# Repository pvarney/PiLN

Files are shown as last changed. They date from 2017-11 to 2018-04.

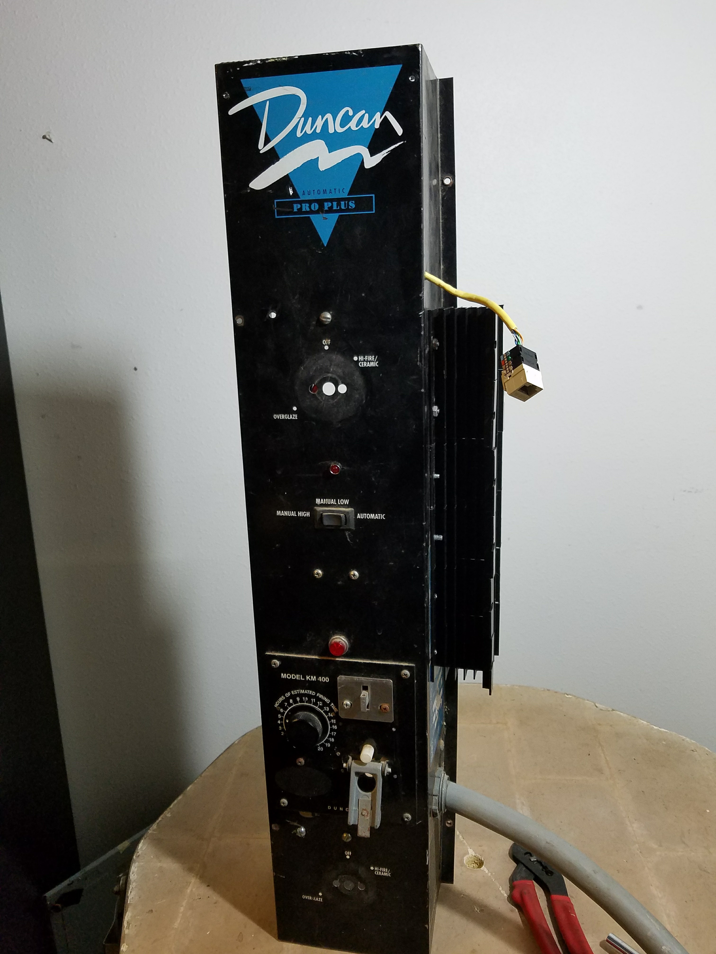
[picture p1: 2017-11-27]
Hardware2.jpg

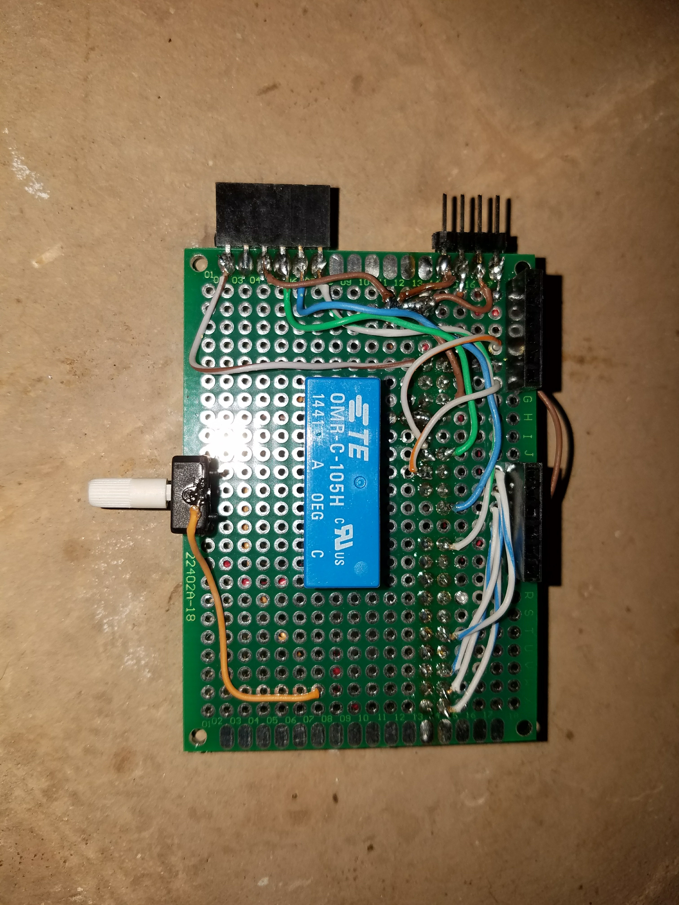
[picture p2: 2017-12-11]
Hardware6.jpg

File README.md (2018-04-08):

# PiLN
Web-based Raspberry Pi Kiln Control Application

This is my first foray into Python, Git, RPi, etc - Please be kind ;-)

I have a good size 220v 45amp electric kiln that has the old "kiln-sitter" style temperature control with bi-metal on/off cycle adjustment knobs. I wanted something with much more precise temperature control for more consistent results and in order to do more work with glass. I started this project with an Arduino board but found the wifi connectivity and coding much too complicated. Being rather proficient in Perl, it seemed the RPi was a better solution. I wrote the original PID control in Perl, but then ported to Python since there seemed to be much more support for it on the RPi and since it was something I wanted to learn anyway.

WARNING! Electricity and heat are dangerous! Please be careful and seek professional help if you are not experienced dealing with high voltage and heat. Use this code/information at your own risk.

This is what I hoped to accomplish:

- Create a PID controller in Python to control an electric kiln. The program takes target temperature, rate, hold time and interval seconds as inputs.
- Daemonize it
- Use MySQL to track temperature change, firing profiles, etc
- Chart the results of firing in real time with google charts
- Wrap in all in a web front end

Many many many thanks to all those who post helpful tidbits out on the web - those on stackoverflow.com in particular. Way to many bits and pieces to give any particular credit. However, I did pull PID calculation code from the following to replace my own code that was iffy (what's math?). It was in C, but was an easy port to Python:

http://brettbeauregard.com/blog/2011/04/improving-the-beginner%E2%80%99s-pid-reset-windup/

All comments, questions, contributions and suggestions welcome!

Future improvements:
- Better calculation of remaining segment time. Currently, remaining time is reset to hold time once temperature is reached.
- Crash/loss of power recovery
- Overheat shutdown

Install:
- Hardware: Raspberry Pi 3, MAX31855 thermocouple interface from Adafruit (https://www.adafruit.com/product/269), High temperature (2372 F) type K thermocouple (http://r.ebay.com/a4cHY1 - search for "kiln thermocouple"), 6 x 40amp Solid State Relays - 2 for each heating element (http://a.co/8PtFgIr), 4 x 20 LCD Display (https://www.adafruit.com/product/198), 5v reed or solid state relay (low voltage load) used to switch 5v supply to high load SSRs (note that the 5v reed relay I used is switched successfully using the 3.3v supply of the GPIO pins), LED for relay on indicator, resistor for LED, variable resistor for LCD contrast adjustment.

- Pin-Out:

		MAX31855+:		3.3v, Pin 1
		MAX31855-:		GROUND, Pin 20
		MAX31855 CLK:		GPIO 25, Pin 22
		MAX31855 CS:		GPIO 24, Pin 18
		MAX31855 DO:		GPIO 18, Pin 12
		REED RELAY+: 		GPIO 4, Pin 7
		REED RELAY-:		GROUND, Pin 20
		REED RELAY INPUT: 	5v, Pin 2
		REED RELAY OUTPUT:	To LED, and high power SSRs (see Fritzing diagram)
		LCD Vss: 		GROUND, Pin 20
		LCD Vcc: 		5v, Pin 2
		LCD Vo: 		Variable Resistor
		LCD RS: 		GPIO 17, Pin 11
		LCD R/W: 		GROUND, Pin 20
		LCD E:			GPIO 27, Pin 13
		LCD DB4:		GPIO 12, Pin 32
		LCD DB5:		GPIO 16, Pin 36
		LCD DB6:		GPIO 20, Pin 38
		LCD DB7:		GPIO 21, Pin 40
		LCD LED+:		5v, Pin 2
		LCD LED-:		GROUND, Pin 20

- Install PiLN files in /home and create log directory:

		cd /home
		sudo git clone https://github.com/pvarney/PiLN
		sudo mkdir /home/PiLN/log
		
- Install MySQL/PHPMyAdmin (PHPMyAdmin not required):

		sudo apt-get install mysql-server
		sudo apt-get install mysql-client php5-mysql
		sudo apt-get install phpmyadmin
		
- Set up Apache for PHPMyAdmin if required. Edit /etc/apache2/apache2.conf and add the follow at the bottom of the file:
	
		Include /etc/phpmyadmin/apache.conf
		
- Set up directories/link for web page:

		sudo mkdir /var/www/html/images	
		sudo mkdir /var/www/html/style	
		sudo ln -s /home/PiLN/images/hdrback.png /var/www/html/images/hdrback.png	
		sudo ln -s /home/PiLN/images/piln.png /var/www/html/images/piln.png	
		sudo ln -s /home/PiLN/style/style.css /var/www/html/style/style.css
	
- Add the following ScriptAlias and Directory parameters under "IfDefine ENABLE_USR_LIB_CGI_BIN" in /etc/apache2/conf-available/serve-cgi-bin.conf:
	
		ScriptAlias /pilnapp/ /home/PiLN/app/
		  <Directory "/home/PiLN/app/">
		    AllowOverride None
		    Options +ExecCGI -MultiViews +SymLinksIfOwnerMatch
		    Require all granted
		  </Directory>

- Create links to enable cgi modules:
	
		cd /etc/apache2/mods-enabled
		sudo ln -s ../mods-available/cgid.conf cgid.conf
		sudo ln -s ../mods-available/cgid.load cgid.load
		sudo ln -s ../mods-available/cgi.load cgi.load

- Restart Apache:
	
		sudo systemctl daemon-reload
		sudo systemctl restart apache2
		
- Install required Python packages:
		
		sudo apt-get install python-mysqldb
		sudo apt-get install python-dev
		sudo pip install PyMySQL
		
- Install Adafruit MAX31855 Module:

		cd ~
		git clone https://github.com/adafruit/Adafruit_Python_MAX31855.git
		cd Adafruit_Python_MAX31855
		sudo python setup.py install		
		
- Required Python modules (separate installs were not required for these using the latest Raspian build as of July 2017): cgi, jinja2, sys, re, datetime, pymysql, json, time, logging, RPi.GPIO.

- Log into the MySQL command line, create the database, create the user and give permissions, then load PiLN.sql to build table structures:

		mysql -uroot -p
		mysql> create database PiLN;
		mysql> CREATE USER 'piln'@'localhost' IDENTIFIED BY 'p!lnp@ss';
		mysql> GRANT ALL PRIVILEGES ON PiLN.* TO 'piln'@'localhost';
		mysql> use PiLN;
		mysql> source /home/PiLN/PiLN.sql;

- To enable automatic startup of the daemon (Had to do the copy/enable/delete/link in order to get systemctl enable to work):

		cp /home/PiLN/daemon/pilnfired.service /etc/systemd/system/
		sudo systemctl daemon-reload
		sudo systemctl enable pilnfired
		sudo rm /etc/systemd/system/pilnfired.service
		sudo ln -s /home/PiLN/daemon/pilnfired.service /etc/systemd/system/pilnfired.service
		sudo systemctl daemon-reload
		sudo systemctl start pilnfired
		sudo systemctl status pilnfired
	I also had to convert mysqld to start up from systemd so that I could set a "want" for pilnfired (mysqld.service file from https://gist.github.com/thomasfr/e4e4bb64352ee574334a):
	
		cp /home/PiLN/daemon/mysqld.service /etc/systemd/system/
		sudo systemctl daemon-reload
		sudo systemctl enable mysqld
		
- Tuning: I spent a while adjusting the PID parameters to get the best results and am still tuning. Your tuning parameters will depend on your specific application, but I used the following which might be a good starting point:

		Proportional:	6.00
		Integral:	0.04
		Derivative:	0.00
	I also had good results setting the interval seconds to 10

Using the Web App:
- On the same network that the RPi is connected to, go to http://<RPi_IPAddress>/pilnapp/home.cgi
From there, I hope it's all fairly self-explanatory. Feel free to contact me with questions!

UPDATE 4/8/2018:
I had a problem with one of the heating elements not working and found that the SSRs couldn't hold up to the heat - even with the heat sinks. I have since replaced them with mechanical relays (same type that were in it before I ripped the guts out). I am now using a 4 relay module to switch on/off the 220v coil voltage on the relays. I also put the MAX31855 module in its own metal box to see if it would reduce the amount of temperature fluctuation.

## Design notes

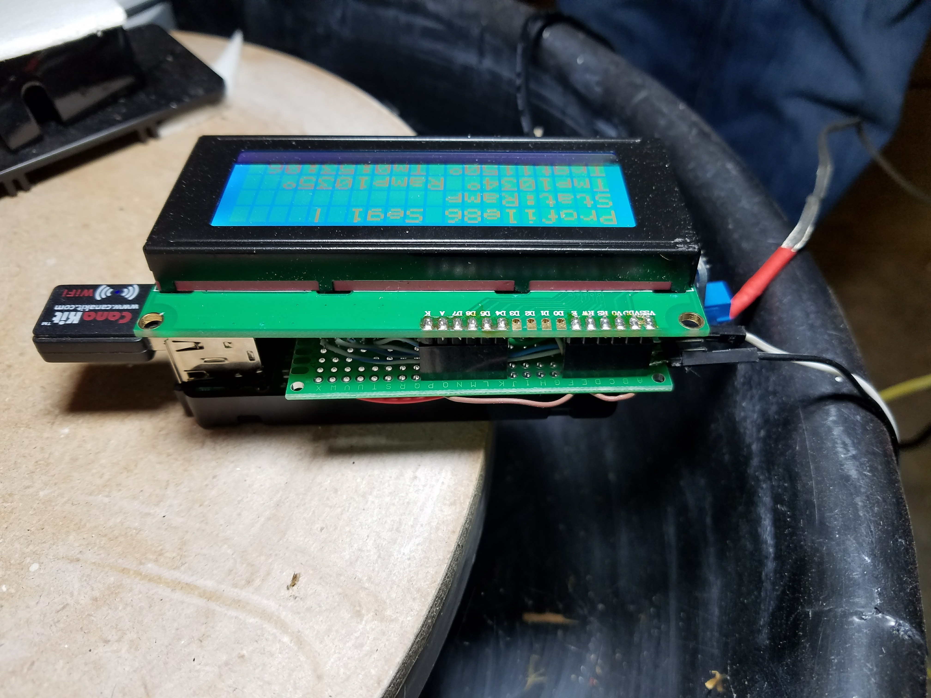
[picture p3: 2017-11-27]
Hardware5.jpg

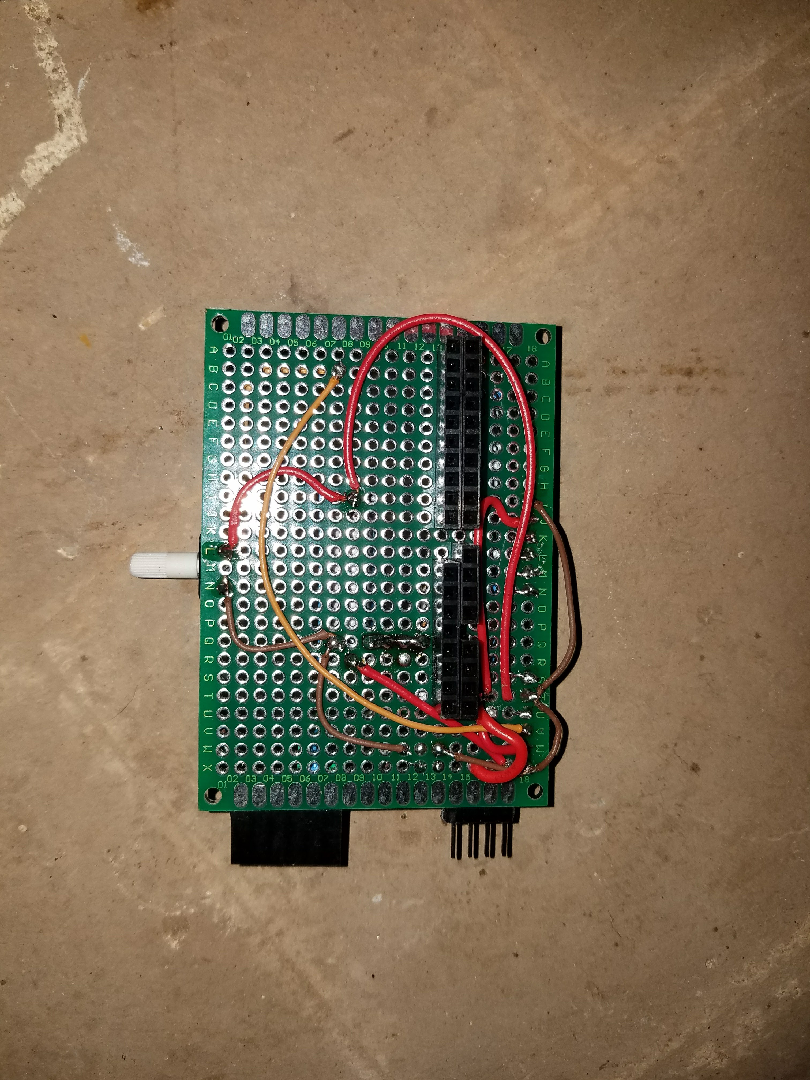
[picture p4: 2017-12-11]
Hardware7.jpg

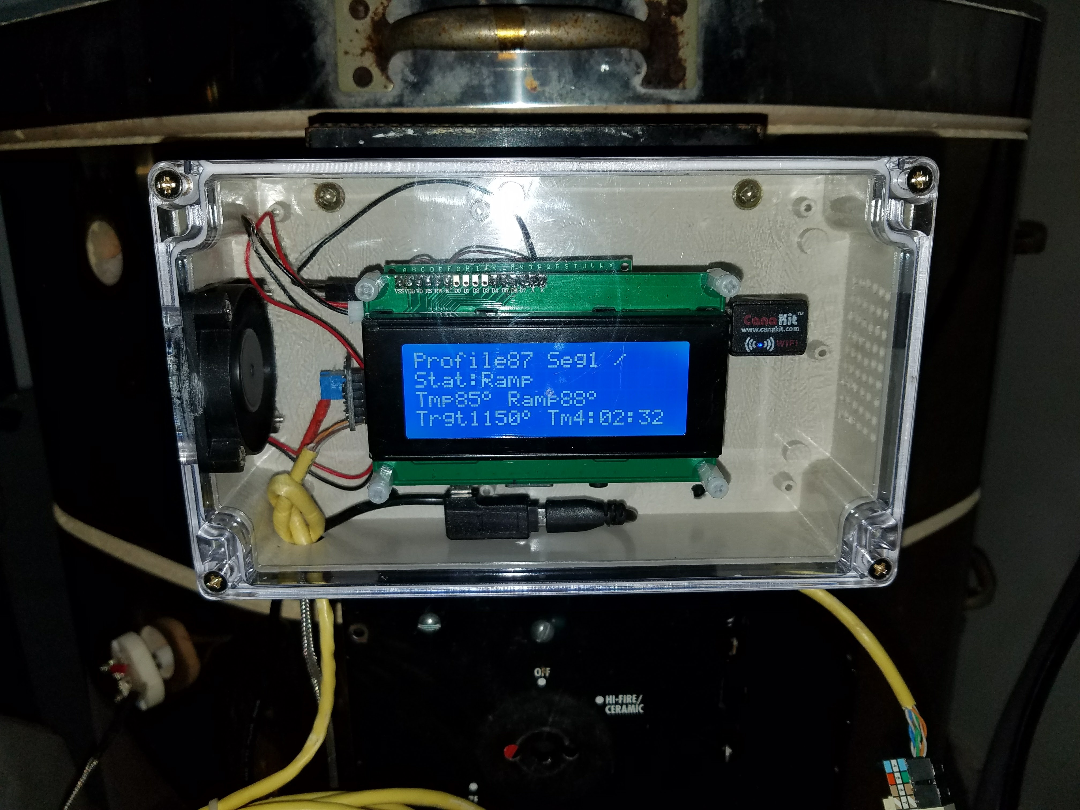
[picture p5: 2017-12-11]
Hardware8.jpg

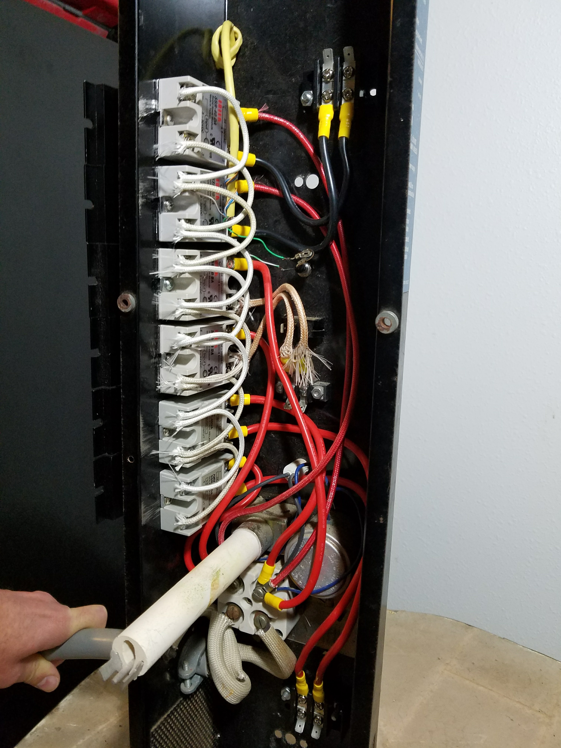
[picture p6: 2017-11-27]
Hardware1.jpg

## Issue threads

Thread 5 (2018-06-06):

ssr heat

BlakeCLewis, 2018-06-06:
Do you think the SSR over heated due to the close proximity to kiln heat? Or heat buildup due to current draw?

pvarney, 2018-06-06:
Probably some of both. I did over engineered the SSRs and used 6 x 40 amp for a kiln that only draws 45 amps, so I think it did have more to do with the kiln heat. If I did it again, I would definitely have the SSRs in a separate unit. Thanks for the comment! I figured no one had even since this thing yet.

BlakeCLewis, 2018-06-06:
I just picked up 2 skutt kilns. Well, I made 2 kilns, 3 section each from
the parts. One I am converting to gas. The other I plan to do a rpi
controller. Though I did see a gas kiln project where they printed gears
for the gas valve and ran it with a pi.
I have looked over you code, but I didn't find the minimum on time for the
he elements. What is the minimum cycle time?

Thanks for the well documented project,
Blake

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

pvarney, 2018-06-09:
You can set the cycle time in the web interface. I'm not sure that's what you're looking for or not. My (not necessarily correct) definition of cycle time is the time interval at which the temperature is checked and a new PID value is calculated. And then depending on the PID output, the elements are turned on for a percentage of the cycle time. I have been using 10 seconds and it seems to work out well. Although I really haven't done a whole lot of experimenting.  Experimenting time went into getting the PID parameters dialed in. I imagine any change to the cycle time would require re-tuning the PID.  Let me know of you end up using any of my code. I haven't had any feedback as of yet, but have done nothing to promote it either.

Thanks!

- Patrick

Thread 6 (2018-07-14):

Two Zones Kiln -- 2 Heat Elements and 2 Thermocouples, possible?

agusting, 2018-07-14:
Hi! first of all thank you for sharing your project.
I have a Kiln with 2 heating elements and a controller that has to be set up mannually and would like to use PiLN to replace it so I can Program it.
My Kiln has two zones with two thermocouples and would like to know if you think it could be easy to usel PiLN to control both Zones in order to have better control of the temperature.

Thanks in advance!

pvarney, 2018-07-18:
Interesting.  The easiest thing to do off the top of my head would be to have 2 separate daemons, databases and web front ends. Are you looking to have different temperatures in the different zones? If not, it wouldn't be too hard to take the average of the thermocouples and have the heating element control be the same for both zones.

pvarney, 2018-07-18:
And you're welcome and sorry for taking so long to get back to you.

agusting, 2018-07-19:
Great!
I'll try to give it a shot.
I'll let you know how it goes.

Do you think it would be possible to run 2 Daemons from 1 RaspberryPi?

Regards

*Agustín Goya*
Editor (EDA)

WANCAMP | POST
tel. +54 11 4857 9083

cel. +54 9 11 15 6545 2427
Skype. agustingoya
agustin@wancamp.com.ar <andres@wancamp.com.ar>
wancamp.com.ar <http://www.wancamp.com.ar/>

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

pvarney, 2018-07-30:
Yes, but I think you'd have to do a lot of renaming for each to work in its own. You could try running just one database, but I'm thinking it would have issues. If you do give it a try,  let me know how it turns out or if I can be of any help.

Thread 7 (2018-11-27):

pilnfired.py in Fire() line 206 in your master branch

BlakeCLewis, 2018-11-27:
Patrick,
      if math.isnan(ReadTmp) or ( abs( ReadTmp - LastTmp ) > ( 2 * Window ) ) or ReadTmp == 0 or ReadTmp > 2400:
        ReadTmp = LastTmp

    I am having problems with the second condition '( abs( ReadTmp - LastTmp ) > ( 2 * Window ) )'. It is a comparison of a temp differential to the time segment.  Could you explain what it is for?
With this condition, my fork always reports erroneous temps to the json file.

I thing that 'ReadTmp == 0' would be better 'ReadTmp == 32' or 'ReadCTmp == 0':
  zero being an error condition of Sensor.readTempC() which CtoF(0) = 32F.

#----------------------------------------------

My fork/branch 'https://github.com/BlakeCLewis/MyPiLN'
    Rearranging, condensing and formatting is my method of trying to understand a program someone else wrote.
   Switched out the LCD to a pioled from adafruit.com. I plan on abstracting the display into a module or function to make it easier to switch in other displays. The pioled is tiny, but it is what I had.
   Switched out MySQL for sqilte3. sqlite3 is a very small, with no daemon. Chrome and Firefox use it for settings, history, cookies and more. It is not multi-user friendly as it does table locks to write. I am currently running a headless pi-zero w. I may go to a Pi 3B+ and run the browser locally, or stay with the  zero, run X without a manager and auto start the browser full screen. Lighttp and FastCGI may help reduce footprint.

Blake

pvarney, 2018-11-29:
Hi Blake. Thanks for reaching out again. It's been a while since I looked at the code (moved to a new house and the kiln isn't hooked up yet). I put that line in to avoid occasional nan and other conditions that would pop up. I think that specific condition was meant to skip over large temperature fluctuations. However, I can't tell you what my thought process was. I want to say that I was shooting for anything greater than 20% difference. But I do remember thinking that a simple percent was not adequate due to how the temperature ramps at lower temps versus higher temps. I'm not sure how using the window variable made sense - it's possible that it's completely arbitrary and worked well for the specific time window I was using. At least now you know the purpose. Let me know if you come up with something better. Do you have your kiln(s) running yet?

BlakeCLewis, 2018-11-29:
I have done 2 bisque fires in the jen-ken w/o controller. In the gas
conversion kiln, I did a test fire(glaze) with 20lb tank and 1 burner, but
iced up at 1080C. I bought 100lb tank, 2 burners and made a few mods, but
have not finished to fire again.
  To your code the biggest change I want to make is add the kiln sitter as
a sensor to end the peak segment. Then set the target thermocouple temp at
1 cone higher for safety cut off.
  I think I understand most of your code. Thanks for making it available. I
like the structure. I think I might add htpasswd and https. Another mod: To
run a profile, a copy is made and the copy is run. This makes the original
usable without having to manually copy the used profile to new runid.

I am a database administrator at the University of Missouri.

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

pvarney, 2018-11-29:
Oh nice! You're not far from me then - I live in Northwest Arkansas and do remote IT work - Primary with Tivoli Storage Manager/Spectrum Protect (IBM's enterprise backup/recovery software). Let me know how it all goes and if you have any more questions.

pvarney, 2018-12-02:
So I got my kiln all hooked up and started a test run but was having problem with it showing the right temp. Started looking at the code and ended up at that line you pointed out. I guess I hadn't fully tested that because the logic is just stupid. On the first loop, the LastTmp variable is zero, so that problem statement would be something like:
  abs ( 60 - 0 ) > ( 2 * 10 )
Which would always be true and therefore always set the ReadTmp to LastTmp which is zero. Thanks for being kind about that. I'm going to remove that part of the if statement for now.

pvarney, 2018-12-02:
Also, I noticed I left the logging in debug, which I generally like, but it puts a lot of extra junk in the log when it's not running a profile. To disable, comment this line (line 55):
level=L.DEBUG,

BlakeCLewis, 2019-02-04:
pvarney,
I have done a few firings in my Skutt ks1027. Old elements, but they are
still moving good at cone6.
I have new elements, but want to get the repairs and some experimentation
done before installing them.
I added a gpio pin using the kiln sitter as a sensor, so when the ks
triggers, it does the hold time at current temp and then goes on to the
next segment (max temp is safety for ks).
If it reaches programmed temp first it does the hold at that temp. (ks is
safety for max temp).
3 bisque firings and 1 glaze firing. I am using relays, one for each ring,
they are same manufacture/series that Skutt sells. DPDT instead of SPDT.

I see that the D is Kd(current_temp - last_temp). I think it should be
Kd(current_error - last_error). if error increases, term is +, if error
decreases term is -.

 Blake

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

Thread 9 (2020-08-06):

I've been updating everything to python3...

fayena, 2020-08-06:
I've a fork of your project that uses the max31856 instead of the max31855 using some code from  BlakeCLewis and the lighttpd server.    https://github.com/fayena/PILN

It was using some depreciated libraries which broke with the last update, so I've been updating and moving everything to python3, circuit python, and the official Adafruit libraries for the max31836.

The snag I've hit is that when go to load the web pages with python3, all I get is the source code.   With python2 everything loads fine.   The only difference is setting python2 to load home.cgi  instead of python3 in the lighttpd.conf file.   It seems to be some snag with Jinja2 (which I did install with pip3) and python3  but it's not throwing any errors.

I'm not at all familiar with jinja2 and since you where the original author of the template files I was hoping you may have some ideas?

fayena, 2020-08-07:
I think I figured it out.

 `print (hdr.encode("utf8") + bdy.encode("utf8") + ftr.encode("utf8"))`  Breaks the rendering in python3

`print (hdr + bdy + ftr)`    Seems to work fine but I haven't gotten all the code updated to do a full test, just the first page.     The rest will have to wait until tomorrow.

fayena, 2020-08-10:
Yep changing those lines of code seems to work just dandy.

pvarney, 2020-08-10:
Glad you figured it out. I can't remember why the utf8 encoding was needed or if it was just part of some snippet I picked up somewhere. My kiln is dormant again because we moved again. I might be looking at your code when it's time to fire things back up.

fayena, 2020-08-11:
I think I've gotten everything updated to python3 and the official adafruit libraries for the max31856.   I need to do one last clean install to verify the install script has no errors.    I recently forked a max31855 branch for a friend but it haven't tested it.

Most of the code is still your code.  I did add a few things and took a few things from Blake C. Lewis.   The biggest thing I added was the install script.

Today I've  worked a bit on adding some code that will text a phone number when a segment is complete and when the firing is done.   Nothing fancy but the test code is working.

Thanks so writing the original code and helping with things.

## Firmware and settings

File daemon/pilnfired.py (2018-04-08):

#!/usr/bin/env python

from signal import *
import os
import time
import math
import logging as L
import sys
import MySQLdb
import RPi.GPIO as GPIO
import Adafruit_MAX31855.MAX31855 as MAX31855
import RPi.GPIO as GPIO
from RPLCD import CharLCD

#Set up LCD
lcd = CharLCD(pin_rs=17, pin_rw=None, pin_e=27, pins_data=[12, 16, 20, 21],
              numbering_mode=GPIO.BCM,
              cols=20, rows=4, dotsize=8,
              auto_linebreaks=True)

lcd.create_char(1, [0b01100,
                    0b10010,
                    0b10010,
                    0b01100,
                    0b00000,
                    0b00000,
                    0b00000,
                    0b00000])
lcd.create_char(2, [0b00000,
                    0b10000,
                    0b01000,
                    0b00100,
                    0b00010,
                    0b00001,
                    0b00000,
                    0b00000])

#Wait for LCD to start up - otherwise you get garbage
time.sleep(1)

# Set up MySQL Connection
SQLHost = '127.0.0.1'
SQLUser = 'piln'
SQLPass = 'p!lnp@ss'
SQLDB   = 'PiLN'
AppDir  = '/home/PiLN'

#Status File
StatFile = '/var/www/html/pilnstat.json'

# Set up logging
LogFile = time.strftime( AppDir + '/log/pilnfired.log' )
L.basicConfig(
  filename=LogFile,
  level=L.DEBUG,
  format='%(asctime)s %(message)s'
)

# Global Variables
#LastErr  = 0.0
#Integral = 0.0
ITerm = 0.0
LastProcVal = 0.0
SegCompStat = 0
LastTmp  = 0.0
wheel = '-'

# MAX31855 Pins/Setup
CLK = 25
CS  = 24
DO  = 18
Sensor = MAX31855.MAX31855(CLK, CS, DO)

# Pin setup for relay
GPIO.setup(4, GPIO.OUT) ## Setup GPIO Pin 7 to OUT
GPIO.output(4,False) ## Turn off GPIO pin 7

def clean(*args):
  print "\nProgram ending! Cleaning up...\n"  
  GPIO.output(4,False) ## Turn off GPIO pin 4
  lcd.close(clear=True)
  time.sleep(0.5)
  GPIO.cleanup() # this ensures a clean exit  
  print "All clean - Stopping.\n"
  os._exit(0)

for sig in (SIGABRT, SIGINT, SIGTERM):
    signal(sig, clean)

# Celsius to Fahrenheit
def CtoF(c):
  return c * 9.0 / 5.0 + 32.0

  
# PID Update
def Update ( SetPoint, ProcValue, IMax, IMin, Window, Kp, Ki, Kd ):

  L.debug( "Entering PID update with parameters SetPoint:%0.2f, ProcValue:%0.2f, IMax:%0.2f, IMin:%0.2f," %
    ( SetPoint, ProcValue, IMax, IMin ))
  L.debug( "  Window:%d, Kp: %0.3f, Ki: %0.3f, Kd: %0.3f" %
    ( Window, Kp, Ki, Kd ))

  global ITerm, LastProcVal

  Err = SetPoint - ProcValue
  ITerm+= (Ki * Err);

  if ITerm > IMax:
    ITerm = IMax
  elif ITerm < IMin:
    ITerm = IMin

  DInput = ProcValue - LastProcVal

  #Compute PID Output
  Output = Kp * Err + ITerm - Kd * DInput;
  if Output > IMax:
    Output = IMax
  elif Output < IMin:
    Output = IMin

  #Remember for next time
  LastProcVal = ProcValue


  L.debug(
    "Exiting PID update with parameters Error:%0.2f, ITerm:%0.2f, DInput:%0.2f, Output:%0.2f" %
    ( Err, ITerm, DInput, Output )
  )

  return Output



#  global LastErr, Integral
#
#  Err      = SetPoint - ProcValue
#
#  Pterm    = Kp * Err
#
#  Dterm    = Kd * ( Err - LastErr )
#  LastErr  = Err
#
#  Integral+= Err
#  if Integral > IMax:
#    Integral = IMax
#  elif Integral < IMin:
#    Integral = IMin
#  Iterm = Ki * Integral
#
#  Output = Pterm + Iterm + Dterm
#
#  L.debug(
#    "Exiting PID update with parameters Error:%0.2f, Integral:%0.2f, Pterm:%0.2f, Iterm:%0.2f, Dterm:%0.2f, Output:%0.2f" %
#    ( Err, Integral, Pterm, Iterm, Dterm, Output )
#  )
#
#  if Output > 100:
#    Output = 100
#  elif Output < 0:
#    Output = 0
#  if Output < 0:
#    Output = 0
#
#  return Output


# Loop to run each segment of the firing profile
def Fire(RunID,Seg,TargetTmp,Rate,HoldMin,Window,Kp,Ki,Kd):

  L.info( "Entering Fire function with parameters RunID:%d, Seg:%d, TargetTmp:%d, Rate:%d," % ( RunID, Seg, TargetTmp, Rate ))
  L.info( "  HoldMin:%d, Window:%d" % ( HoldMin, Window ))

  global SegCompStat
  global wheel

  HoldSec  = HoldMin * 60
  RampMin  = 0.0
  RampTmp  = 0.0
  ReadTmp  = 0.0
  LastTmp  = 0.0
  StartTmp = 0.0
  TmpDif   = 0.0
  Steps    = 0.0
  StepTmp  = 0.0
  StartSec = 0.0
  EndSec   = 0.0
  NextSec  = 0.0
  RunState = "Ramp"
  Cnt      = 0
  RampTrg  = 0
  ReadTrg  = 0
  
  while RunState != "Stopped" and RunState != "Complete":

    if time.time() >= NextSec:
      Cnt += 1
      NextSec = time.time() + Window

      # Get temp
      LastTmp   = ReadTmp
      ReadCTmp  = Sensor.readTempC()
      ReadTmp   = CtoF(ReadCTmp)
      ReadCITmp = Sensor.readInternalC()
      ReadITmp  = CtoF(ReadCITmp)
      if math.isnan(ReadTmp) or ( abs( ReadTmp - LastTmp ) > ( 2 * Window ) ) or ReadTmp == 0 or ReadTmp > 2400:
        ReadTmp = LastTmp

      if RampTrg == 0:
        RampTmp += StepTmp

      if TmpDif > 0:

        # Ramp temp reached target
        if RampTmp >= TargetTmp and RampTrg == 0:
          RampTmp = TargetTmp
          RampTrg = 1
          if ReadTrg == 1:
            RunState = "Ramp complete/target temp reached"
          else:
            RunState = "Ramp complete"

        # Read temp reached target
        if ( ( TargetTmp - ReadTmp <= TargetTmp * 0.006 ) or ( ReadTmp >= TargetTmp ) ) and ReadTrg == 0:
          ReadTrg = 1
          EndSec = int(time.time()) + ( HoldMin * 60 )
          L.info( "Set temp reached - End seconds set to %d" % EndSec )
          if RampTrg == 1:
            RunState = "Ramp complete/target temp reached"
          else:
            RunState = "Target temp reached"

      elif TmpDif < 0:

        # Ramp temp reached target
        if RampTmp <= TargetTmp and RampTrg == 0:
          RampTmp = TargetTmp
          RampTrg = 1
          if ReadTrg == 1:
            RunState = "Ramp complete/target temp reached"
          else:
            RunState = "Ramp complete"

        # Read temp reached target
        if ( ( ReadTmp - TargetTmp <= TargetTmp * 0.006 ) or ( ReadTmp <= TargetTmp ) ) and ReadTrg == 0:
          ReadTrg = 1
          EndSec = int(time.time()) + ( HoldMin * 60 )
          L.info( "Set temp reached - End seconds set to %d" % EndSec )
          if RampTrg == 1:
            RunState = "Ramp complete/target temp reached"
          else:
            RunState = "Target temp reached"

      if StartTmp == 0:
        StartTmp = ReadTmp
        StartSec = int(time.time())
        NextSec  = StartSec + Window
        TmpDif   = TargetTmp - StartTmp
        RampMin  = ( abs (TmpDif) / Rate ) * 60
        Steps    = ( RampMin * 60 ) / Window
        StepTmp  = TmpDif / Steps
        EndSec   = StartSec + ( RampMin * 60 ) + ( HoldMin * 60 )
        RampTmp = StartTmp + StepTmp
        if ( TmpDif > 0 and RampTmp > TargetTmp ) or ( TmpDif < 0 and RampTmp < TargetTmp ):
          RampTmp = TargetTmp
        LastErr  = 0.0
        Integral = 0.0

#        if TmpDif < 0:
#          RunState = 2

        L.info( "First pass of firing loop - TargetTmp:%0.2f, StartTmp:%0.2f, RampTmp:%0.2f, TmpDif:%0.2f," %
          ( TargetTmp, StartTmp, RampTmp, TmpDif ))
        L.info( "  RampMin:%0.2f, Steps:%d, StepTmp:%0.2f, Window:%d, StartSec:%d, EndSec:%d" %
          ( RampMin, Steps, StepTmp, Window, StartSec, EndSec ) )
    
      #Output = Update(RampTmp,ReadTmp,50000,-50000,Window,Kp,Ki,Kd)
      Output = Update(RampTmp,ReadTmp,100,0,Window,Kp,Ki,Kd)

      CycleOnSec  = Window * ( Output * 0.01 )
      if CycleOnSec > Window:
        CycleOnSec = Window

      RemainSec = EndSec - int ( time.time() ) 
      RemMin, RemSec = divmod(RemainSec, 60)
      RemHr, RemMin  = divmod(RemMin, 60)
      RemainTime = "%d:%02d:%02d" % (RemHr, RemMin, RemSec)
      L.debug( "RunID %d, Segment %d (loop %d) - RunState:%s," % ( RunID, Seg, Cnt, RunState ))
      L.debug( "  ReadTmp:%0.2f, RampTmp:%0.2f, TargetTmp:%0.2f, Output:%0.2f, CycleOnSec:%0.2f, RemainTime:%s" %
        ( ReadTmp, RampTmp, TargetTmp, Output, CycleOnSec, RemainTime )
      )

      if Output > 0:
        L.debug("==>Relay On")
        GPIO.output(4,True) ## Turn on GPIO pin 7
        time.sleep(CycleOnSec)

      if Output < 100:
        L.debug("==>Relay Off")
        GPIO.output(4,False) ## Turn off GPIO pin 7

      # Write statu to file for reporting on web page
      L.debug( "Write status information to status file %s:" % StatFile )
      sfile = open(StatFile,"w+")
      sfile.write('{\n' +
        '  "proc_update_utime": "' + str(int(time.time())) + '",\n' +
        '  "readtemp": "'          + str(int(ReadTmp))     + '",\n' +
        '  "run_profile": "'       + str(RunID)            + '",\n' +
        '  "run_segment": "'       + str(Seg)              + '",\n' +
        '  "ramptemp": "'          + str(int(RampTmp))     + '",\n' +
        '  "targettemp": "'        + str(int(TargetTmp))   + '",\n' +
        '  "status": "'            + str(RunState)         + '",\n' +
        '  "segtime": "'           + str(RemainTime)       + '"\n'  +
        '}\n'
      )
      sfile.close()

      if wheel == '-':
        wheel = '\x02'
      elif wheel == '\x02':
        wheel = '|'
      elif wheel == '|':
        wheel = '/'
      else:
        wheel = '-'
    
      lcd.clear()
      lcd.cursor_pos = (0, 0)
      lcd.write_string(u'Profile' + str(RunID) + ' Seg' + str(Seg) + ' ' + wheel )
      lcd.cursor_pos = (1, 0)
      lcd.write_string(u'Stat:' + str(RunState)[0:14] )
      lcd.cursor_pos = (2, 0)
      lcd.write_string(u'Tmp' +  str(int(ReadTmp)) + '\x01 Ramp' + str(int(RampTmp)) + '\x01' )
      lcd.cursor_pos = (3, 0)
      lcd.write_string(u'Trgt' + str(int(TargetTmp)) + '\x01 Tm' + str(RemainTime) )
      #lcd.write_string(u'Trgt ' + str(int(TargetTmp)) + '\x01,Tm ' )
      #print 'Trgt ' + str(int(TargetTmp)) + ',Tm ' + str(RemainTime)

      L.debug("Writing stats to Firing DB table...")
      SQL = "INSERT INTO Firing (run_id, segment, datetime, set_temp, temp, int_temp, pid_output) VALUES ( '%d', '%d', '%s', '%.2f', '%.2f', '%.2f', '%.2f' )" % ( RunID, Seg, time.strftime('%Y-%m-%d %H:%M:%S'), RampTmp, ReadTmp, ReadITmp, Output )
      try:
        SQLCur.execute(SQL)
        SQLConn.commit()
      except:
        SQLConn.rollback()
        L.error("DB Update failed!")


      # Check if profile is still in running state
      RowsCnt = SQLCur.execute("select * from Profiles where state='Running' and run_id=%d" % RunID)

      if RowsCnt == 0:
        L.warn("Profile no longer in running state - exiting firing")
        SegCompStat = 1 
        RunState = "Stopped"
  
      if time.time() > EndSec and ReadTrg == 1:
        RunState = "Complete"
  
#      L.debug(
#            "RunState:%s, TargetTmp:%0.2f, StartTmp:%0.2f, RampTmp:%0.2f, TmpDif:%0.2f, RampMin:%0.2f, Steps:%d, StepTmp:%0.2f, Window:%d, StartSec:%d, EndSec:%d" %
#            ( RunState, TargetTmp, StartTmp, RampTmp, TmpDif, RampMin, Steps, StepTmp, Window, StartSec, EndSec ) 
#          )



L.info("===START PiLN Firing Daemon===")
L.info("Polling for 'Running' firing profiles...")

while 1:

  # Get temp
  ReadCTmp  = Sensor.readTempC()
  ReadTmp   = CtoF(ReadCTmp)
  ReadCITmp = Sensor.readInternalC()
  ReadITmp  = CtoF(ReadCITmp)
  if math.isnan(ReadTmp):
    ReadTmp = LastTmp

  # Write statu to file for reporting on web page
  L.debug( "Write status information to status file %s:" % StatFile )
  sfile = open(StatFile,"w+")
  sfile.write('{\n' +
    '  "proc_update_utime": "' + str(int(time.time())) + '",\n' +
    '  "readtemp": "'          + str(int(ReadTmp))     + '",\n' +
    '  "run_profile": "none",\n' +
    '  "run_segment": "n/a",\n' +
    '  "ramptemp": "n/a",\n' +
    '  "status": "n/a",\n' +
    '  "targettemp": "n/a"\n' +
    '}\n'
  )
  sfile.close()

  if wheel == '-':
    wheel = '\x02'
  elif wheel == '\x02':
    wheel = '|'
  elif wheel == '|':
    wheel = '/'
  else:
    wheel = '-'
  
  lcd.clear()
  lcd.cursor_pos = (0, 0)
  lcd.write_string(u'IDLE ' + wheel )
  lcd.cursor_pos = (2, 0)
  lcd.write_string(u'Temp ' +  str(int(ReadTmp)) + '\x01')

#{
#  "proc_update_utime": "1506396470",
#  "readtemp": "145",
#  "run_profile": "none",
#  "run_segment": "n/a",
#  "targettemp": "n/a"
#}


  # Check for 'Running' firing profile
  SQLConn = MySQLdb.connect(SQLHost, SQLUser, SQLPass, SQLDB);
  SQLCur  = SQLConn.cursor()
  RowsCnt = SQLCur.execute("select * from Profiles where state='Running'")

  if RowsCnt > 0:
    Data = SQLCur.fetchone()
    RunID = Data[0]
    Kp = float(Data[3])
    Ki = float(Data[4])
    Kd = float(Data[5])
    L.info("Run ID %d is active - starting firing profile" % RunID)

    StTime=time.strftime('%Y-%m-%d %H:%M:%S')
    L.debug("Update profile %d start time to %s" % ( RunID, StTime ) )
    SQL = "UPDATE Profiles SET start_time='%s' where run_id=%d" % ( StTime, RunID )
    try:
      SQLCur.execute(SQL)
      SQLConn.commit()
    except:
      SQLConn.rollback()
      L.error("DB Update failed!")

    # Get segments
    L.info("Get segments for run ID %d" % RunID)
    SQL="select * from Segments where run_id=%d" % RunID
    SQLCur.execute(SQL)
    ProfSegs = SQLCur.fetchall()

    for Row in ProfSegs:
      RunID = Row[0]
      Seg = Row[1]
      TargetTmp = Row[2]
      Rate = Row[3]
      HoldMin = Row[4]
      Window = Row[5]

      if SegCompStat == 1:
        L.debug("Profile stopped - skipping segment %d" % Seg)

      else:
        L.info( "Run ID %d, segment %d parameters: Target Temp: %0.2f, Rate: %0.2f," %
          ( RunID, Seg, TargetTmp, Rate ))
        L.info( "  Hold Minutes: %d, Window Seconds: %d" %
          ( HoldMin, Window ))

        StTime=time.strftime('%Y-%m-%d %H:%M:%S')
        L.debug("Update run id %d, segment %d start time to %s" % ( RunID, Seg, StTime ) )
        SQL = "UPDATE Segments SET start_time='%s' where run_id=%d and segment=%d" % ( StTime, RunID, Seg )
        try:
          SQLCur.execute(SQL)
          SQLConn.commit()
        except:
          SQLConn.rollback()
          L.error("DB Update failed!")
  
        time.sleep(0.5)
        Fire(RunID,Seg,TargetTmp,Rate,HoldMin,Window,Kp,Ki,Kd)
        GPIO.output(4,False) ## Turn off GPIO pin 7
  
        EndTime=time.strftime('%Y-%m-%d %H:%M:%S')
        L.debug("Update run id %d, segment %d end time to %s" % ( RunID, Seg, EndTime ) )
        SQL = "UPDATE Segments SET end_time='%s' where run_id=%d and segment=%d" % ( EndTime, RunID, Seg )
        try:
          SQLCur.execute(SQL)
          SQLConn.commit()
        except:
          SQLConn.rollback()
          L.error("DB Update failed!")

    if SegCompStat == 1:
        L.info("Profile stopped - Not updating profile end time")

    else:
      EndTime=time.strftime('%Y-%m-%d %H:%M:%S')
      L.debug("Update profile end time to %s and state to 'Completed' for run id %d" % ( EndTime, RunID ) )
      SQL = "UPDATE Profiles SET end_time='%s', state='Completed' where run_id=%d" % ( EndTime, RunID )
      try:
        SQLCur.execute(SQL)
        SQLConn.commit()
      except:
        SQLConn.rollback()
        L.error("DB Update failed!")

    SegCompStat = 0

    L.info("Polling for 'Running' firing profiles...")

  SQLConn.close()
  time.sleep(2)

#except KeyboardInterrupt:  
#  print "\nKeyboard interrupt caught. Cleaning up...\n"

#except:  
#  print "\nOther error or exception occurred! Cleaning up...\n"  
  
#finally:  

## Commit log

2017-09-09 Major revision - worked out bugs
    [pilnfired.py]
2017-09-20 Added PID calc reference
2017-09-23 Daemon updates including new PID function
2017-10-01 Added current status to the header
2017-11-27 Update readme
    LCD connections, PID tuning, addiitional parts
2017-11-27 Fritzing Diagram
    [PiLN.fzz]
2018-04-08 Added segment run time to profile run and added some code to correct issues with inaccurate temperature readings
    [pilnfired.py]
